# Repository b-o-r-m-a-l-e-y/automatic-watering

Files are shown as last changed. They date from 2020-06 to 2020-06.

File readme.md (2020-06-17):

# Автополив на ATtiny13

Прошивка написана для микроконтроллера ATtiny13A. Печатная плата и схема для KiCAD находится в соответствующей папке. С кнопкой вышел косяк при разводке печатной платы, её развернуть надо и переразвести, надеюсь поправлю.

Питается от одной банки Li-ion 18650. В схеме предусмотрена микросхема  заряда аккума и контроль напряжения разряда (начнет мигать светодиод D1). В спящем режиме потребляет меньше 10 мкА и просыпается, чтобы проверить влажность почвы

## Маленькая инструкция

Клеммы датчика вставляются в земельку параллельно друг другу, насос со шлангом в воду и подключается аккумулятор. Порог сухости почвы настраивается константой `SOIL_LOW_LIMIT`, которая лежит в пределах от 0 до 255. Если напряжение на аккумуляторе опустится ниже ~3.4В, при каждой проверке светодиод будет моргать 2 раза. Пороговое напряжение задается константой `BATTERY_LOW_LIMIT`. В нормальном режиме один раз моргает светодиодом при проверке датчиков.

## По схеме

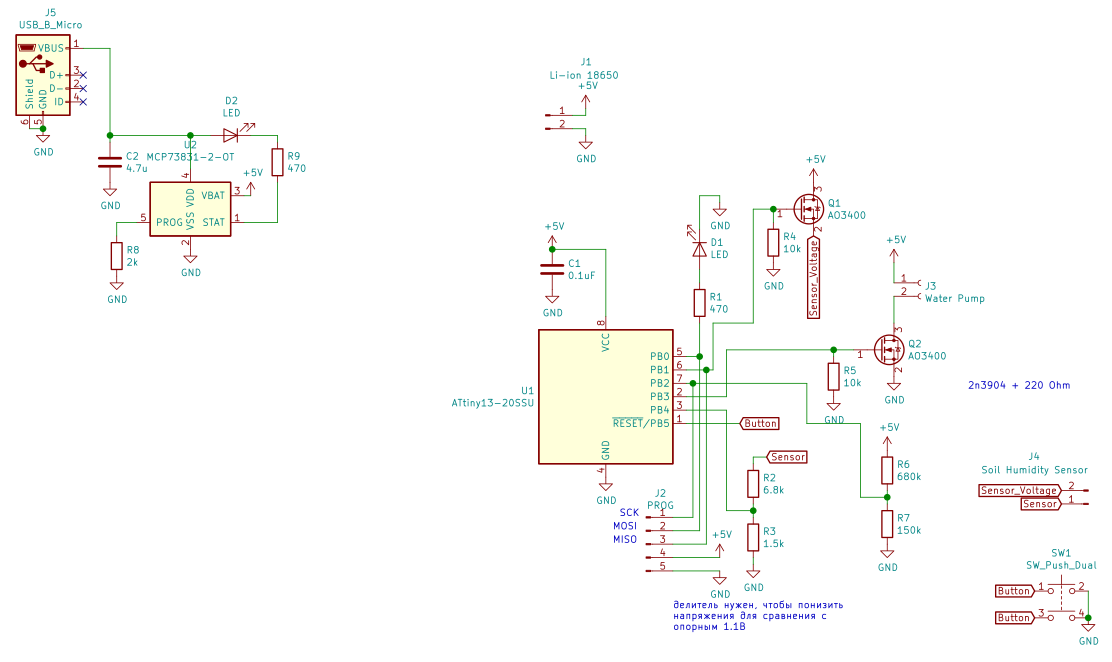
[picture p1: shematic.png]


- Транзистор Q1 нужен, чтобы ток через датчик почвы протекал только в момент измерения (когда транизстор открыт)
- Q2 - включает/выключает насос
- R6/R7 - делитель для сравнения напряжения на батарее с внутренним опорным 1.1В
- R2/R3 - аналогично, но для датчика влажности почвы
- MCP73831 - микросхемка для контроля заряда аккумулятора

## По коду

Собирал компилятором avr-gcc, прошивал при помощи USBasp. Makefile присутствует. FUSE биты стандартные.

Выходит из сна (Power down) каждые 8с по прерыванию от WDG. Инкрементирует счетчик и если он больше значения  `UPDATE_TIME`, то измеряет напряжение на батарейке и на клеммах датчика. При этом моргает один раз светодиодом.

АЦП настроен в режим с левым смещением, младшие разряды опускаются, поэтому разрешение - 8 бит (от 0 до 255).

Для контроля времени включения насоса используется таймер, настроенный на счет миллисекунд. Время включения насоса регулируется константой `WATER_PUMP_TIME_MAX`.

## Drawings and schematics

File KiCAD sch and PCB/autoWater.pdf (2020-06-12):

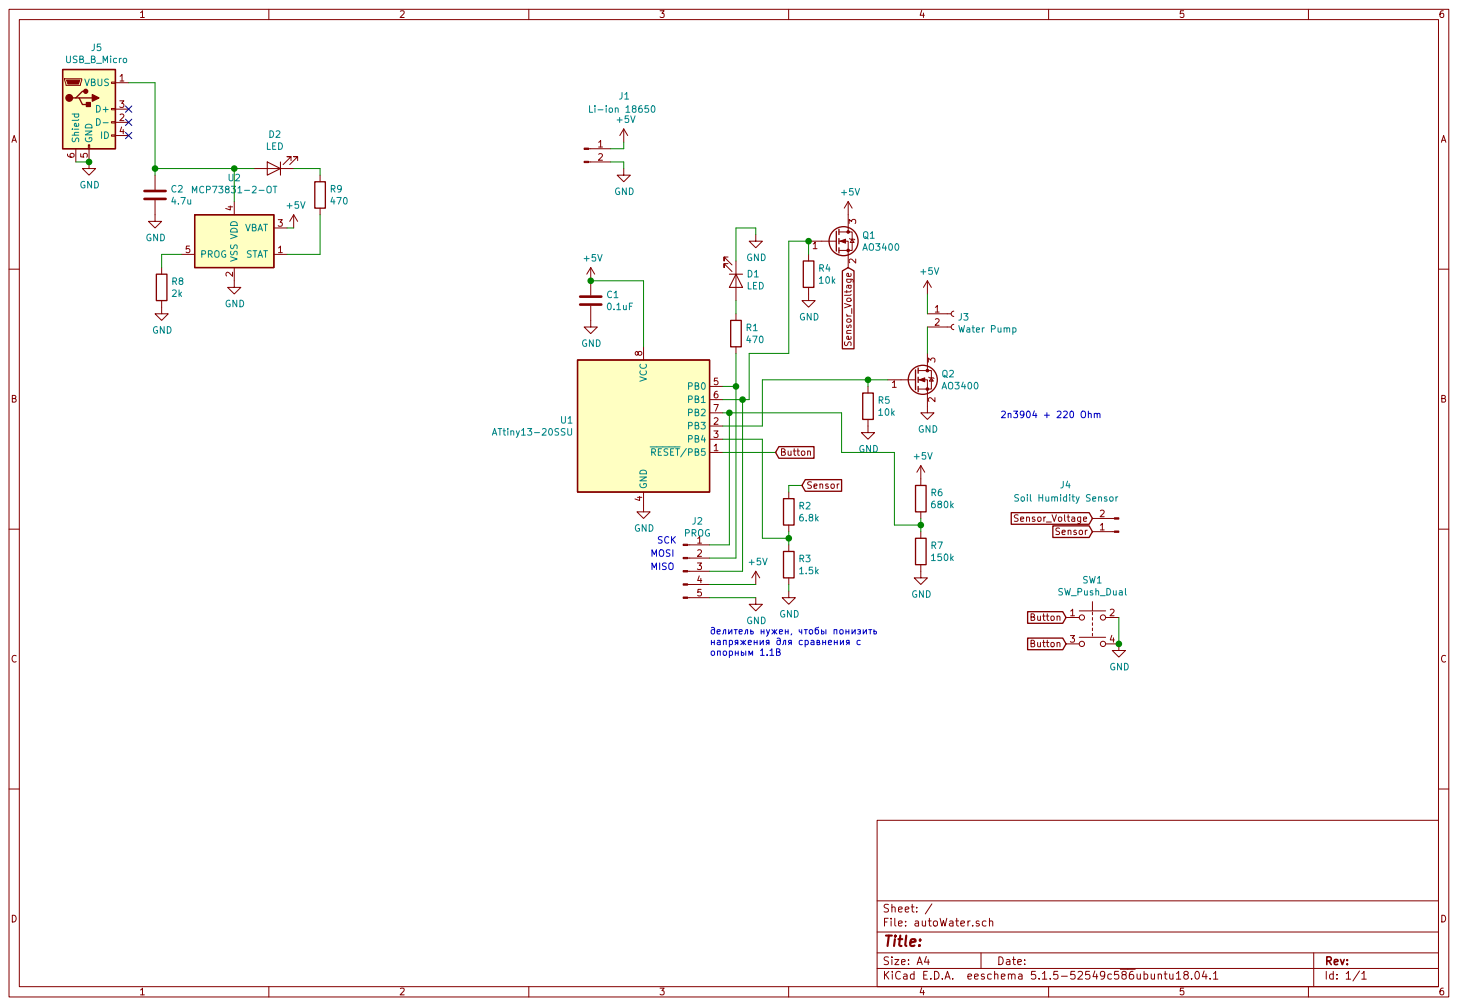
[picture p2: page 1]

Id: 1/1 Title: File: autoWater.sch Sheet: /

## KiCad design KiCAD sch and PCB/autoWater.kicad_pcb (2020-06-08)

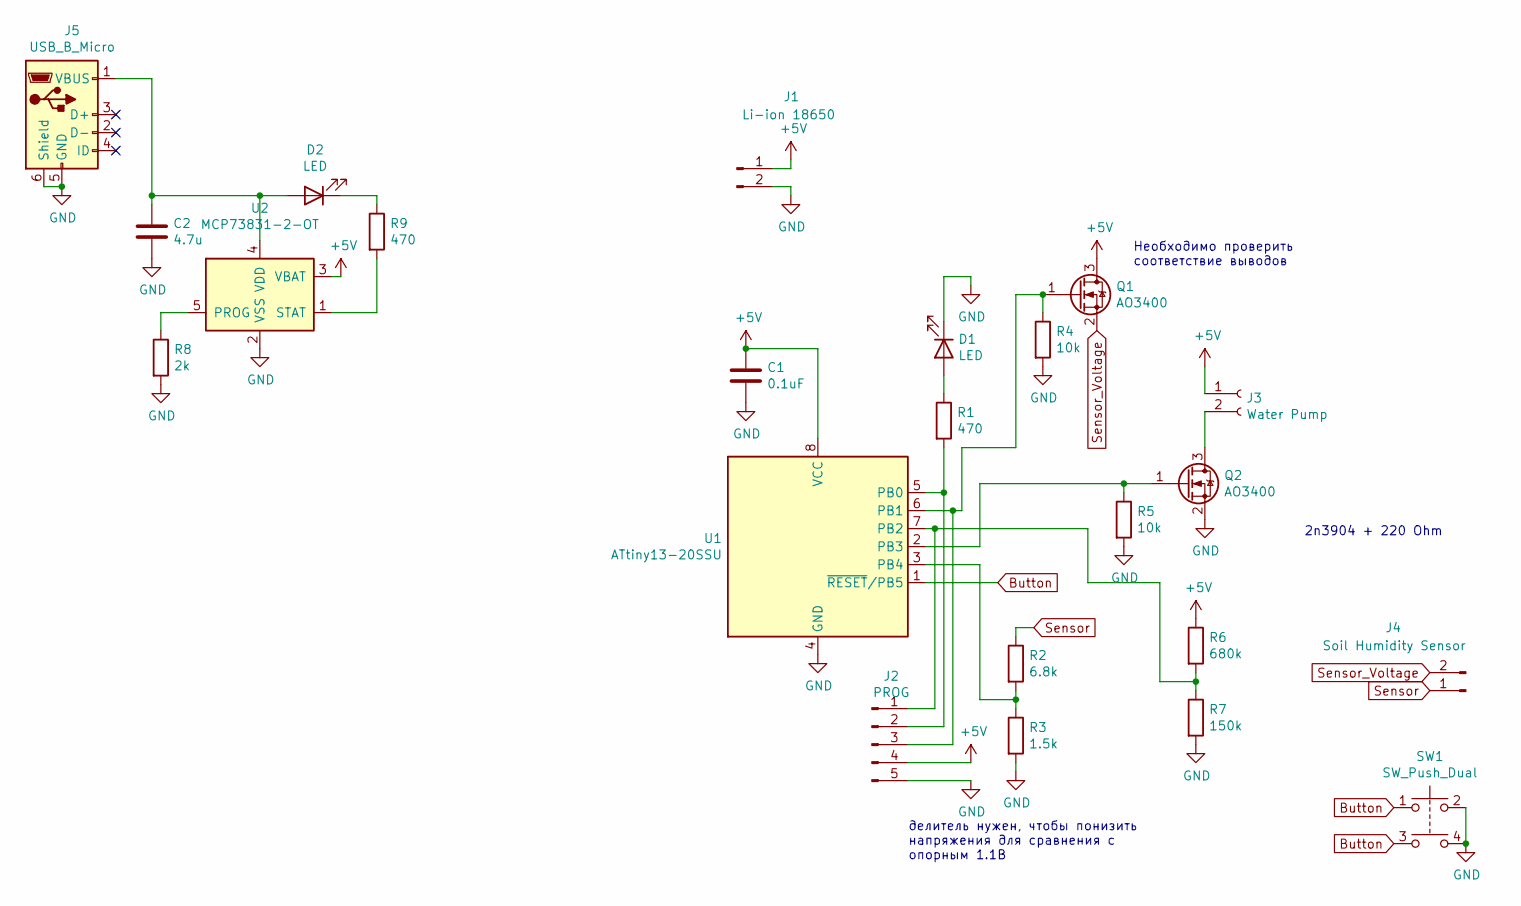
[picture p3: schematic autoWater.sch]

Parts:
C1: 0.1uF; C_0805_2012Metric_Pad1.15x1.40mm_HandSolder
C2: 4.7u; C_0805_2012Metric_Pad1.15x1.40mm_HandSolder
D1, D2: LED; LED_0805_2012Metric_Pad1.15x1.40mm_HandSolder
J1: Li-ion 18650; PinHeader_1x02_P2.54mm_Vertical
J2: PROG; PinHeader_1x05_P2.54mm_Vertical
J3: Water Pump; PinHeader_1x02_P2.54mm_Vertical
J4: Soil Humidity Sensor; PinHeader_1x02_P2.54mm_Vertical
J5: USB_B_Micro; USB_Micro-B_Wuerth_629105150521
Q1, Q2: AO3400; SOT-23
R1, R9: 470; R_0805_2012Metric_Pad1.15x1.40mm_HandSolder
R2: 6.8k; R_Axial_DIN0411_L9.9mm_D3.6mm_P15.24mm_Horizontal
R3: 1.5k; R_Axial_DIN0411_L9.9mm_D3.6mm_P15.24mm_Horizontal
R4, R5: 10k; R_0805_2012Metric_Pad1.15x1.40mm_HandSolder
R6: 680k; R_0805_2012Metric_Pad1.15x1.40mm_HandSolder
R7: 150k; R_0805_2012Metric_Pad1.15x1.40mm_HandSolder
R8: 2k; R_0805_2012Metric_Pad1.15x1.40mm_HandSolder
SW1: SW_Push_Dual; SW_SPST_Omron_B3FS-100xP
U1: ATtiny13-20SSU; SOIC-8_3.9x4.9mm_P1.27mm
U2: MCP73831-2-OT; SOT-23-5

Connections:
+5V: C1.1, J1.1, J2.4, J3.1, Q1.3 (D), R6.1, U1.8 (VCC), U2.3 (VBAT)
Button: SW1.1, SW1.3, U1.1 (~RESET~/PB5)
GND: C1.2, C2.2, D1.1 (K), J1.2, J2.5, J5.5 (GND), J5.6 (Shield), Q2.2 (S), R3.2, R4.2, R5.2, R7.2, R8.2, SW1.2, SW1.4, U1.4 (GND), U2.2 (VSS)
unnamed: C2.1, D2.2 (A), J5.1 (VBUS), U2.4 (VDD)
unnamed: D1.2 (A), R1.1
unnamed: D2.1 (K), R9.1
unnamed: J2.1, R6.2, R7.1, U1.7 (PB2)
unnamed: J2.2, R1.2, U1.5 (PB0)
unnamed: J2.3, Q1.1 (G), R4.1, U1.6 (PB1)
unnamed: J3.2, Q2.3 (D)
unnamed: Q2.1 (G), R5.1, U1.2 (PB3)
unnamed: R2.2, R3.1, U1.3 (PB4)
unnamed: R8.1, U2.5 (PROG)
unnamed: R9.2, U2.1 (STAT)
Sensor: J4.1, R2.1
Sensor_Voltage: J4.2, Q1.2 (S)

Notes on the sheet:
Необходимо проверить соответствие выводов
2n3904 + 220 Ohm
делитель нужен, чтобы понизить напряжения для сравнения с опорным 1.1В

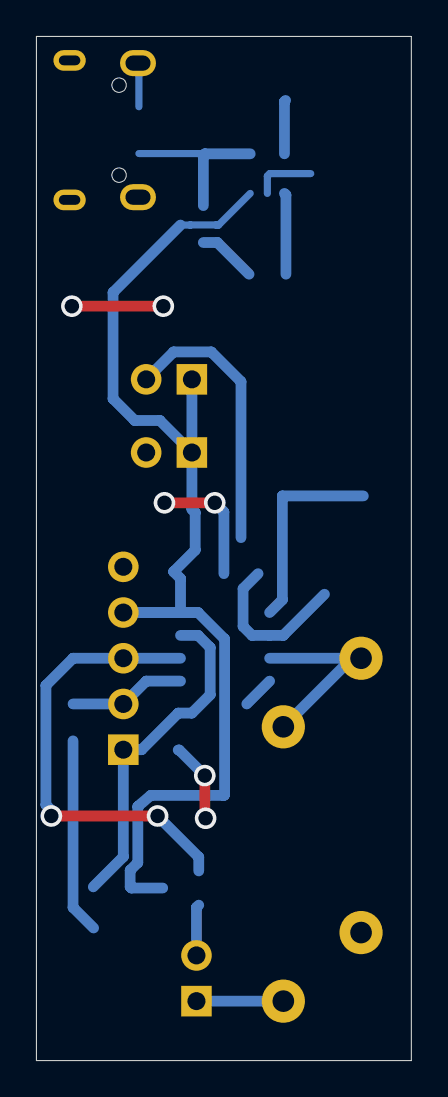
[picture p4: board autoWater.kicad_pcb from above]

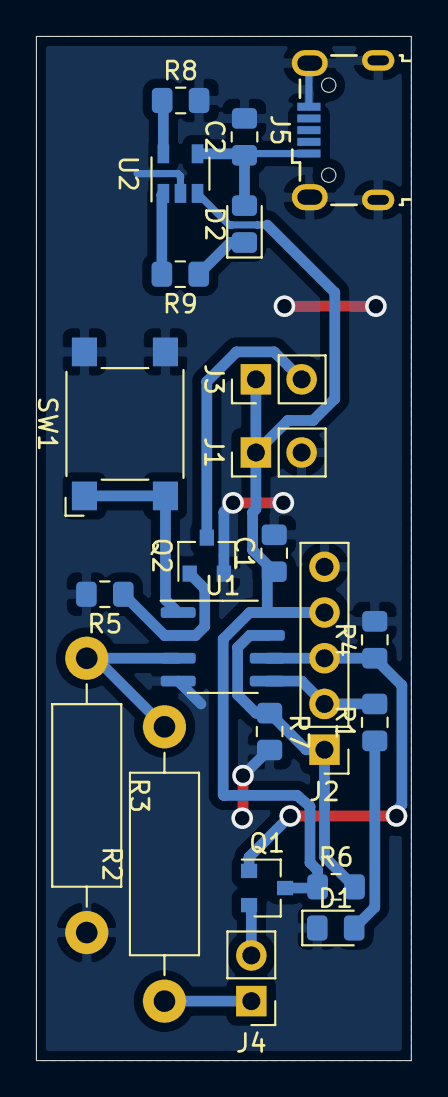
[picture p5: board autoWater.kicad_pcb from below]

Board: 2 copper layers, 20.8 x 56.9 mm, 23 parts (23 on the bottom side), 16 nets.

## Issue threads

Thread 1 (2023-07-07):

fuses

micropythondevel, 2023-07-07:
this correct  fuses ?

AVRDUDE | -U lfuse:w:0xCA:m | -U hfuse:w:0xEE:m | -U lock:w:0xFF:m

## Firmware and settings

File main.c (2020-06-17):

#define __AVR_ATtiny13A__
#define F_CPU 1200000
#include <avr/io.h>
#include <avr/interrupt.h>
#include <avr/sleep.h>
#include <util/delay.h>

/*
 * TODO:
 * Battery LED shold be turned on for some time
 * Disable ADC before sleep
 */

//Freq CPUio 9.6 MHz/8=1.2MHz

//Resistor divider Up = 680k and Down = 200k
#define BATTERY_LOW_LIMIT       140 //The lowest voltage for battery = 3.4 Volts
#define SOIL_LOW_LIMIT          105 //The lower, the more dusty soil is (120 for 5V)

#define WATER_PUMP_TIME_MAX     8000 //How much time water pump os on in milliseconds

#define UPDATE_TIME             3*60*60/8 //Once in 3 hours

uint8_t waterPumpFlag = 0;
uint8_t goToSleepFlag = 0;
volatile uint16_t waterPumpTime = 0;

uint16_t volatile WDT8sCounter = 1; // Varible will be incremented in WDG timer

#define DEBUG_LED_ON        PORTB |= (1<<PORTB0)
#define DEBUG_LED_OFF       PORTB &= ~(1<<PORTB0)
#define DEBUG_LED_TOGGGLE   PORTB ^= (1<<PORTB0)

inline void configuration()
{
    cli();
    DDRB = (1<<PIN0)|(1<<PIN1)|(1<<PIN3);
    //Pull-up for button NEED CORRECT FUSE
    PORTB = (1<<PORTB5);

    MCUSR &= ~(1<<WDRF);
    WDTCR = (1<<WDCE);
    //Watchdog interrupt each 8s
    WDTCR |= (1<<WDP3)|(0<<WDP2)|(0<<WDP1)|(1<<WDP0);
    //Enable WD interrupt
    WDTCR |= (1<<WDTIE);
    WDTCR &= ~(1<<WDE);

    //Disable digital input for PB2 and 4
    DIDR0 |= (1<<ADC2D)|(1<<ADC1D);
    //Enable ADC, Prescaler 128
    ADCSRA = (1<<ADPS2)|(1<<ADPS1)|(1<<ADPS0);
    //ADC internal reference, right adjust PB2 (soil sensor)
    ADMUX = (1<<REFS0)|(1<<ADLAR)|(0<<MUX1)|(1<<MUX0);
    ADCSRA = (1<<ADEN);

    //Timer for 1 ms CTC Mode
    //Enable interrupt on Output Compare Match A
    TIMSK0=(1<<OCIE0A);
    TCCR0A=(1<<WGM01)|(0<<WGM00);
    //Prescaler 8
    TCCR0B=(1<<CS01);
    TCNT0=0;
    OCR0A=150;

    set_sleep_mode(SLEEP_MODE_PWR_DOWN);
    sei();
}

void blink(uint8_t n)
{
    for (uint8_t i=0; i<n; i++)
    {
        _delay_ms(100);
        DEBUG_LED_ON;
        _delay_ms(100);
        DEBUG_LED_OFF;
    }
}

uint16_t getADCResult()
{
    //Start convertion
    ADCSRA |= (1<<ADSC);
    while (ADCSRA & 1<<ADSC) {} //Wait util conversion is complete
    uint16_t data = 0;
    data = ADCH;
    return data;
}

/*
 * Checking battery voltage. If low, light up LED on PB0
 */
void batteryCheck()
{
    uint16_t batVoltage = 0;
    ADMUX |= (1<<MUX0);
    ADMUX &= ~(1<<MUX1);
    batVoltage = getADCResult();
    //Debug LED LOL
    
    if (batVoltage<BATTERY_LOW_LIMIT) blink(2);
    else PORTB &= (~1<<PORTB0);
}

/*
 * Check voltage on resistor divider
 */
void soilSensorCheck()
{
    PORTB |= (1<<PORTB1); //Open transistor for sensor
    uint16_t soilVoltage = 0;
    ADMUX |= (1<<MUX1);
    ADMUX &= ~(1<<MUX0);
    soilVoltage = getADCResult();
    if (soilVoltage<SOIL_LOW_LIMIT) 
    {
        waterPumpFlag=1;
    }
    else blink(1);
    PORTB &= ~(1<<PORTB1); //Close transistor
}

int main()
{
    configuration();
    PORTB |= (1<<PORTB1); //Open transistor for sensor
    uint16_t soilVoltage = 0;
    ADMUX |= (1<<MUX1);
    ADMUX &= ~(1<<MUX0);
    soilVoltage = getADCResult();
    while(soilVoltage<SOIL_LOW_LIMIT)
    {
        soilVoltage = getADCResult();
        PORTB |= (1<<PORTB3); //Turn on water pump
    }
    PORTB &= ~(1<<PORTB3); //Turn off water pump
    PORTB &= ~(1<<PORTB1); //Close sensor transistor
    while(1)
    {
        if (WDT8sCounter>UPDATE_TIME)
        {
            batteryCheck();
            soilSensorCheck();
            blink(1);
            cli();
            WDT8sCounter=0;
            sei();
        }
        if(waterPumpFlag)
        {
            PORTB |= (1<<PORTB3); //Turn on water pump
            if(waterPumpTime>WATER_PUMP_TIME_MAX)
            {
                PORTB &= !(1<<PORTB3);
                cli();
                waterPumpFlag=0;
                waterPumpTime=0;
                goToSleepFlag=1;
                sei();
            }
        }
        else goToSleepFlag = 1;
        if(goToSleepFlag) 
        {
            //DEBUG_LED_ON;
            cli();
            sleep_enable();
            ADCSRA &= ~(1<<ADEN);
            sei();
            sleep_cpu();
            ADCSRA |= (1<<ADEN);
            waterPumpTime = 0;
            goToSleepFlag = 0;
            //DEBUG_LED_OFF;
        }
    }
    return 0;
}

ISR(TIM0_COMPA_vect)
{
    cli();
    if(waterPumpFlag) waterPumpTime++;
    else waterPumpTime = 0;
    sei();
}

ISR(WDT_vect)
{
    cli();
    WDT8sCounter++;
    sei();
}

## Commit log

2020-05-14 some shematic changes
    [autoWater.kicad_pcb, autoWater.sch]
2020-05-21 some sch changes
    [autoWater.kicad_pcb, autoWater.sch]
2020-05-26 some commit
    [autoWater.kicad_pcb, autoWater.sch]
2020-06-02 new pcb
    [autoWater.kicad_pcb]
2020-06-03 added mi ion charger on pcb
    [autoWater.kicad_pcb, autoWater.sch]
2020-06-03 added li ion charger on pcb
    [autoWater.kicad_pcb, autoWater.sch]
2020-06-03 resistor value change
    [autoWater.kicad_pcb, autoWater.sch]
2020-06-07 add timer service
2020-06-09 text on sch
    [autoWater.sch]
2020-06-12 add readme & small code changes
    [autoWater.sch]
2020-06-17 some fixes, time & blink
    [main.c]
